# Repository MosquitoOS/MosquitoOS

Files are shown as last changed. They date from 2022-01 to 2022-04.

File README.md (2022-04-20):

# MosquitoOS

Ceci est le répertoire du projet Mosquito Opensource.

A l'exeption des composants vélos (roues, pédalier, moyeux, freins, etc.) tous les composants du Mosquito sont sous licence libre `CERN Open Hardware Licence Version 2 - Weakly Reciprocal`.

Consommables		                    Observations	                                                    fournisseur			
epoxy		                            Epoxy Resin L + Hardener CL (60 min) kit/ 930 g non cytotoxique	    https://shop1.r-g.de/en/art/109285-AP		
charges fibres cellulose pour collages	                        		                                    sicomin			
colle SADER vinylique a bois rapide exterieur	9.1	collage cp sur styrodur	magasin bricolage			
tresse verre diametre 20mm x5m			                                                                    https://shop1.r-g.de/en/art/201100			
tresse fibre de verre diametre 45mm x5m			                                                            https://shop1.r-g.de/en/art/201105
ruban carbone UD 250g/sqm 25mm 10m			                                                                https://shop1.r-g.de/en/art/200159-25			
DPP™ Carbon rectangular rod (10.0 x 1.0) 1000 mm x4	                                                        https://shop1.r-g.de/en/art/750302					
demoulant PVA 250ml 						
ruban peel ply 20mm 100m						
tissus fin verre 55g/sqm 10m		    pour marouflage sur carenage carton	                                https://shop1.r-g.de/en/art/G-0055097-LW
pinceau agent demoulage						
spatules			                                                                                        https://shop1.r-g.de/en/art/325100
rouleau essuis tout (industriel)						
gants 					
tissus d'arachage et scotch et film retractable						
mousse styrodur		                    plaque magasin bricolage ep 20mm env 10 euros				
contre plaque marine ou aviation	    95.12euros	cp aviation 1500x500mm ep1.5 prix=45euros+port, 1.5m2 devrait suffire	https://jr-contreplaque.fr			
plaque carton ep 2 ou 3mm		        env 7m2 pour le carenage				
scotch papier pour carton						
plaque carton epaisse (nidabeille)pour les couples		ep15mm plaque 800x600 env4 plaques 5euros/plaque	
Colle loctite 648 pour ficher les roulements								https://www.scootfast.net/loctite-bearing-sealant-5-ml.html

plaques aluminium 1 et 1.5mm			https://www.blockenstock.fr/epaisseur-5-8mm-c102x3032238			
tube alu diam25 lg 1m		            pour direction et divers				
tube diam22.2	                        recup velo				

boulons, divers quincaillerie						
6 rotules M8 LH et 6 rotules M8 RH	25.4 Euros sur ebay.co.uk provenance chine 3euros piece	remarque bis : prendre du M6 moins cher moins lourd			
tige filetee M8 LH	5	                5euros/250mm chine				
tige filetee M8 RH	5					
6 ecrous a gauche M8	                6.78 Euros Metric RH / LH Threaded Half Nuts Ideal for Rod End Rose Joint - Packs x5 or x10			
roulements a billes 37x25x7 6805-2rs	8 Euros	ebay ou 123roulements.fr			
charnieres a billes x4	                23 Euros	2pcs Door Hinge Durable Ball Bearing Thickened Stainless Steel Replacement Parts	ebay			
impression plans A0	                    netprinter.co.uk			
						
matos velo						
1 cadre vtt 26" bases et haubans cintres	40	leboncoin				
1 jeu de pedalier square taper	0	recup sur vtt mbk le boncoin				
1 pedalier (manivelles courtes) 	30					
plateau 130bcd env 42 dents	0					
2 pedales						
1 chaine						
1 pignon pour nexus	15	a confirmer				
1 moyeu nexus rollerbrake	30	remarque 150euros si neuf port compris inclus pignon poignee tournante et ecrous				
switching unit for nexus 8 	15	besoin reference exacte				
rondelles de sécurité pour des pattes de cadre verticales (bleue 8R / verte 8L)						
1 jeu de direction		provenant du cadre vtt 				
1 potence reglable longue (type tandem passager)		ou bien stratification sur tube alu				
1 guidon hamster		idem, bricolage de tubes				
ou 1 guidon carbone a recouper modifier						
2 poignees de frein 						
1 repartiteur de freinage		a fabriquer				
1 changement de vitesse pour nexus						
2 poignees mousse ou guidoline de guidon						
3 gaines de freins + 3 cables de freins 						
1 gaine de derailleur et cable de derailleur		sur le cadre de vtt				
4 tendeurs ajustage tension de cable frein et derailleurs						
2 jantes 20" 28H pour roue arriere	40	jante exal tx19				
1 jante 20" 32ou36H? pour nexus						
56rayons roue arriere et 56 tetes de rayon laiton	23	0.45euro/piece				
32 ou 36 rayons roue avant						
2 moyeux freins a tambour sturmey archer	140	70euros piece				
2 axes inox pour roue arriere 						
3 chambres a air						
3 pneus						
						
total appros	927.6 Euros					

Information issue de https://ethercalc.net/budget-workshop-mosquito

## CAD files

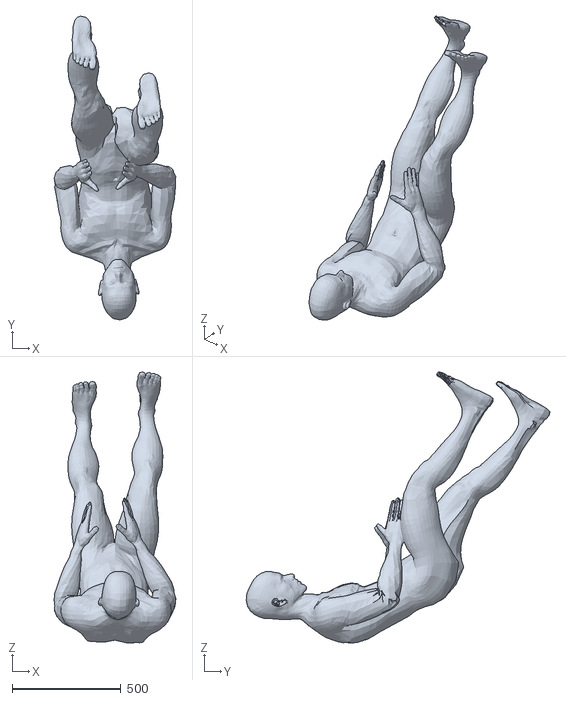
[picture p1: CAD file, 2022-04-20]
dorian3d_recumbent_position.stl
559.3 x 1394.2 x 1244.1

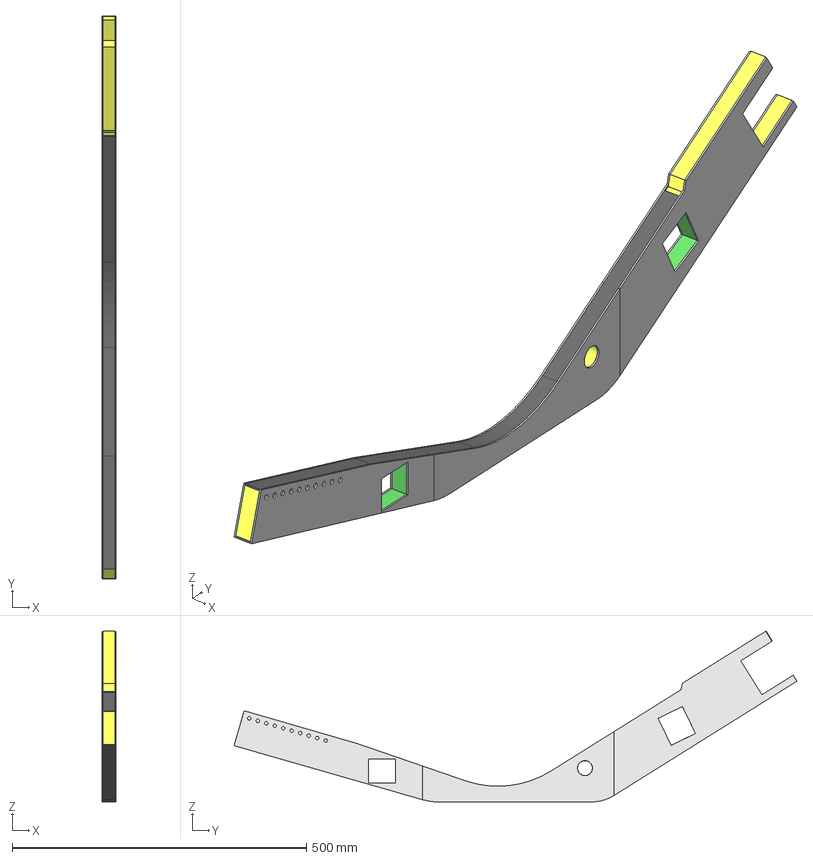
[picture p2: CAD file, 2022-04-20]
longerontempWIP.FCStd
24.0 x 956.3 x 290.5 mm
mousse
Tasseau06
Support_axe_biellettes
Tasseau04
Tasseau03
Tasseau05
Tasseau02
Tasseau01
Carbone_bas
Carbone_Haut
Cp_avant
Cp_milieu
Cp_arriere

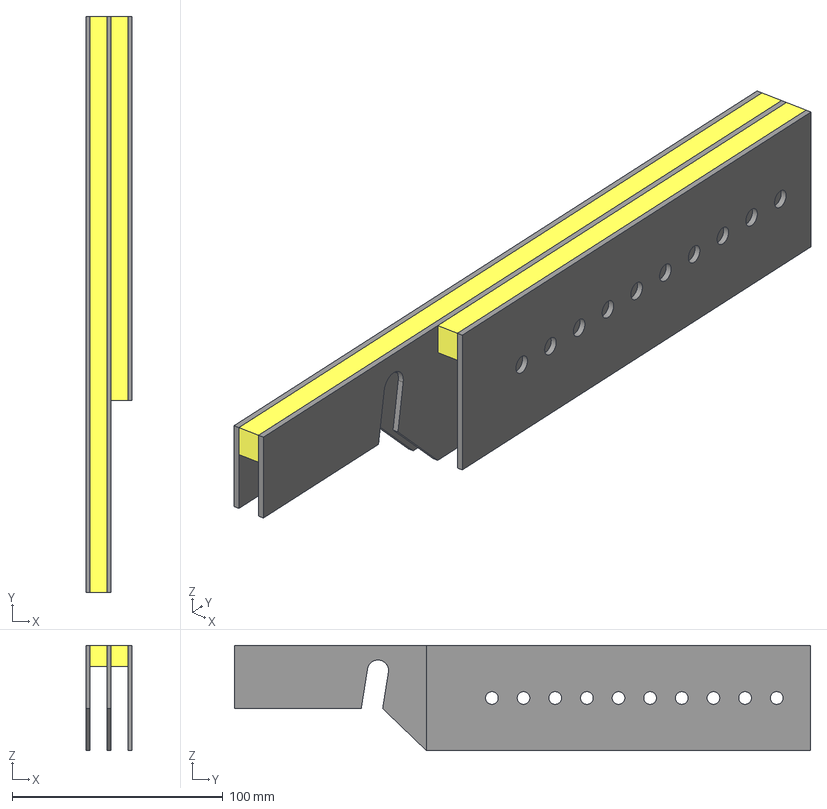
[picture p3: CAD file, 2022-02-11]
patte_avant_gauche_support_roue_avant.FCStd
22.0 x 273.0 x 50.0 mm
Tasseau01
Long_alu_peau_01_02
Tasseau_06
Court_Alupeau_03

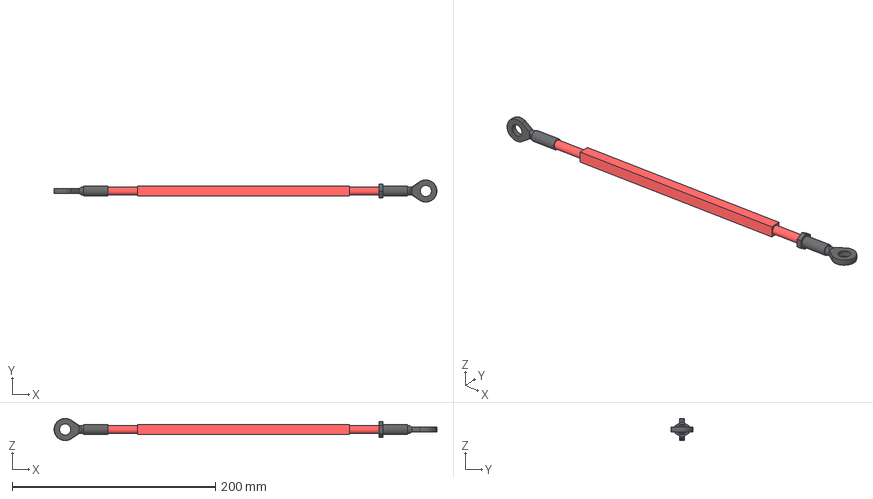
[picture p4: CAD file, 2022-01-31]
bielle_grande_(355_mm_entre_axe).FCStd
377.0 x 21.9 x 21.9 mm
Bout de bielle
Partie centrale de la bielle
Bout de bielle 2

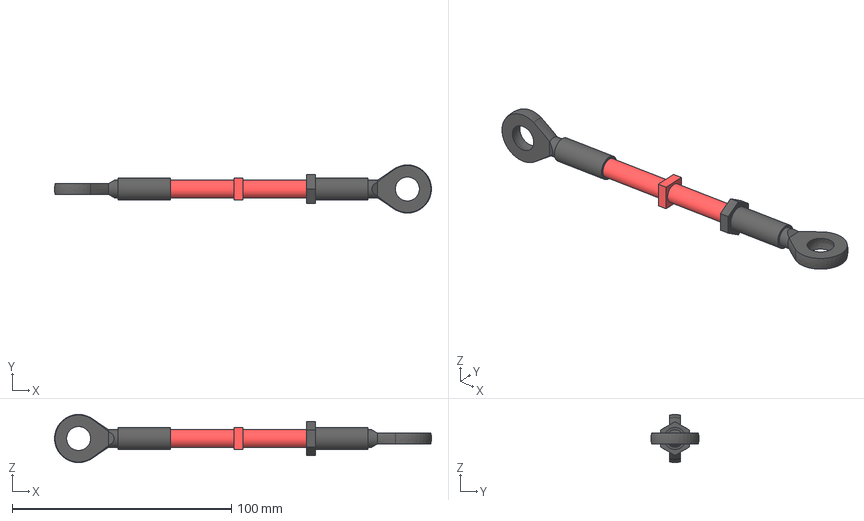
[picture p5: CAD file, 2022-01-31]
bielle_(150_mm_entre_axe).FCStd
172.0 x 21.9 x 21.9 mm
Bout de bielle
Partie centrale de la bielle
Bout de bielle 2

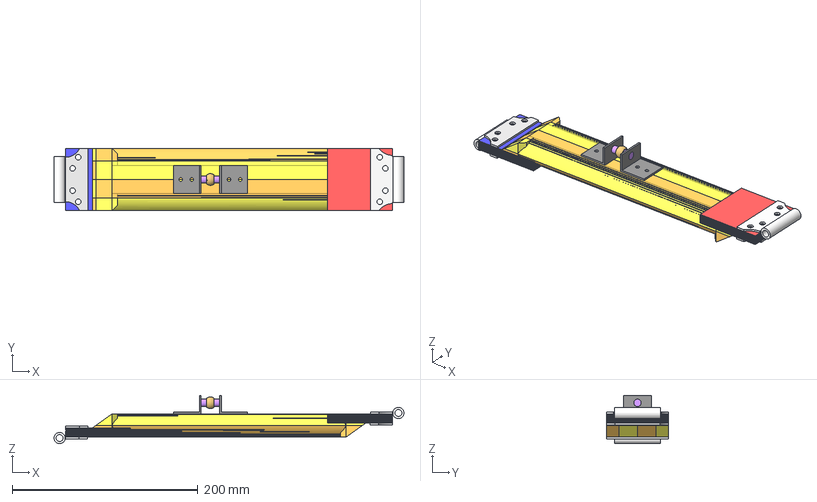
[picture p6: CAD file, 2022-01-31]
barre_de_direction.FCStd
377.0 x 67.0 x 52.0 mm
Barre de direction (corps)001
Pièce d'extrémité 2 N°3/010
Pièce d'extrémité 1 N°7/010
Pièce d'extrémité 1 N°6/010
Pièce d'extrémité 1 N°1/010
Pièce d'extrémité 2 N°8/010
Pièce d'extrémité 2 N°5/010
Pièce d'extrémité 1 N°4/010
Ogive de bielle002
Charnière 003
Piece contrefort de la charnière 003
Pièce d'extrémité 1 N°8/010
Pièce d'extrémité 1 N°9/010
Piece contrefort de la charnière 004
Ogive de bielle003
Cornière 004
Cornière 003
Charnière 004
Pièce d'extrémité 2 N°4/010
Pièce d'extrémité 2 N°6/010
Pièce d'extrémité 1 N°2/010
Pièce d'extrémité 2 N°2/010
Pièce d'extrémité 2 N°9/010
Pièce d'extrémité 2 N°1/010
Pièce d'extrémité 2 N°7/010
Axe de l'ogive001
Pièce d'extrémité 1 N°5/010
Tasseau 1
Tasseau 2
Tasseau 3
Tasseau 4
Tasseau 5
Tasseau 6
Tasseau 7
Tasseau 8

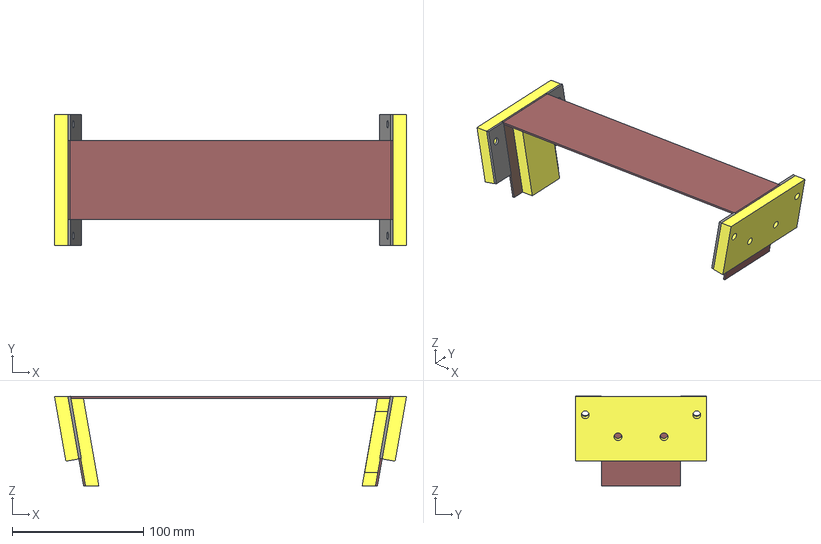
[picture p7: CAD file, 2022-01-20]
attache_bielle_alternative.FCStd
268.3 x 100.0 x 68.4 mm
Tasseau_bois
Cp_exterieur001
Cp_exterieur002
Cp_bois_10mm_ep
Tasseau_bois003
Body009 (mirrored)
Alu_2mm
Alu_2mm001

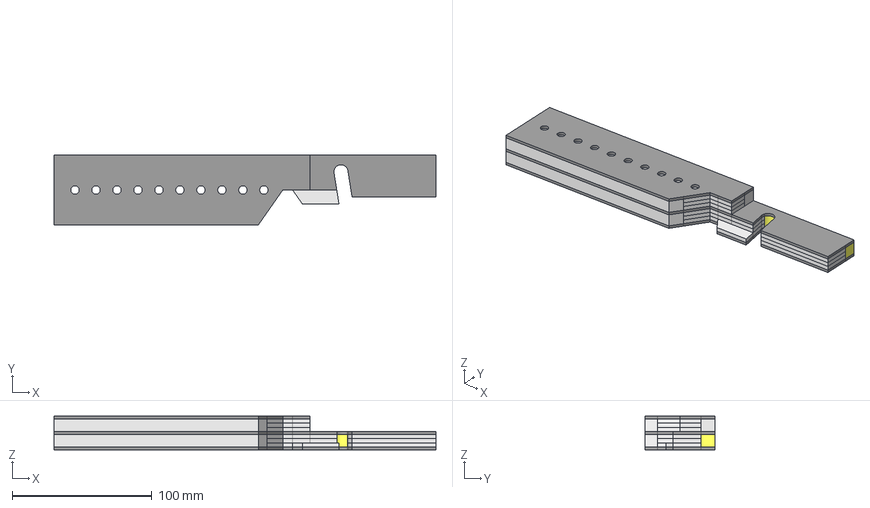
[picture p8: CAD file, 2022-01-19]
patte_avant_droite.FCStd
273.0 x 50.0 x 24.0 mm
cp_45_deg_1.1
aluminium_ext
aluminium_inter
semelle_supp_1
cp_0_deg_1.1
cp_45_deg_2
semelle_inf_1
cp_90_deg_2
aluminium_milieu
cp_90_deg_1.1
cp_90_deg_1.002
cp_45_deg_1.002
cp_0_deg_1.002
semelle_inf_002
semelle_supp_002
cp_0_deg_2

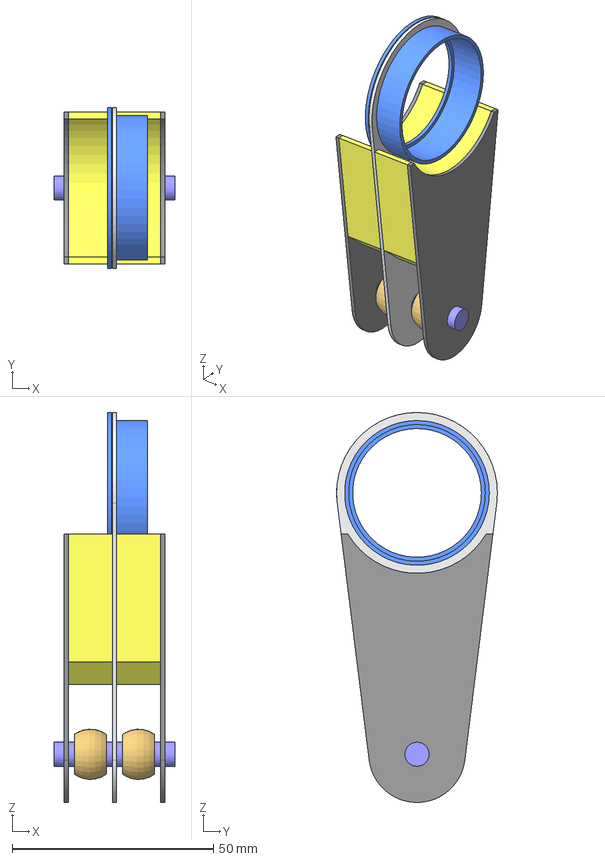
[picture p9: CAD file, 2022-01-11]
guignol_intermediaire.FCStd
30.0 x 40.0 x 97.0 mm
Pièce centrale
Pièce annexe 1
Pièce d'extrémité 1
Pièce annexe 2
Pièce d'extrémité 2
Ogive de bielle
Ogive de bielle (clone)
Goupille
Piece de maintien sur le roulement

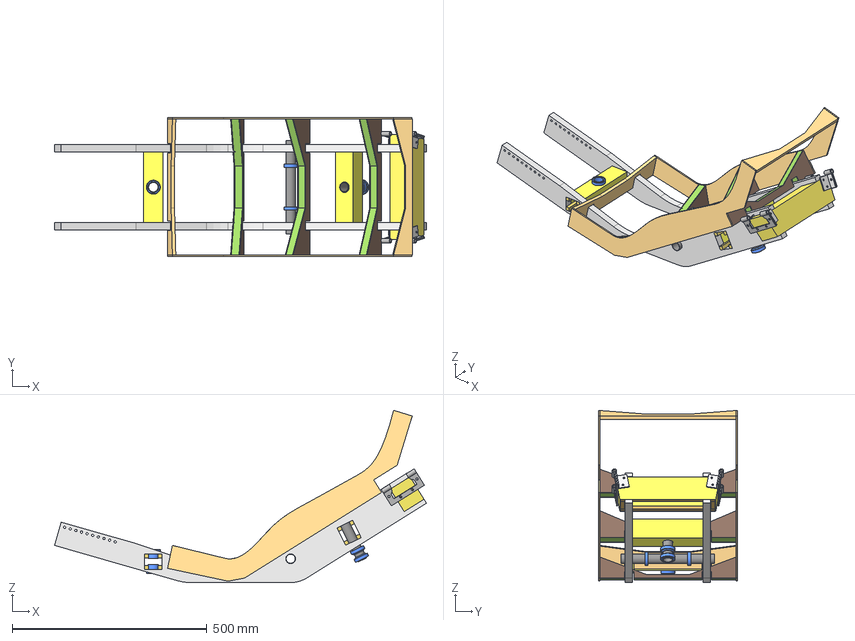
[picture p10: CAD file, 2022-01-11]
chassis_du_trike.FCStd
954.0 x 356.0 x 442.1 mm
traverse
Roulement 003
Roulement 004
traverse haut
Tasseaux intérieurs 1
Tasseaux intérieurs 2
Cornière 1
copie de cornière1
Cornière 2
Copie de cornière 2
Charnière
Charnière clone
Tasseau intèrieur 3
Tasseau intèrieur 4
Tasseau005
Enveloppe001
Tasseau006
Tasseau007
Tasseau008
Roulement
Roulement clone
Tasseau
Enveloppe
Tasseau2
Tasseau3
Tasseau4
Axe central
Roulement 1
Roulement 2
corps du longeron
longeron 2 clone0
Couple01
Longerons_siege
Longeron02_CP_01
Longeron02_mousse
Longeron02_CP_02
Longeron03_CP_01
Longeron03_mousse
Longeron03_CP_02
Longeron04_CP_01
Longeron04_mousse
Longeron04_CP_02
Longeron05

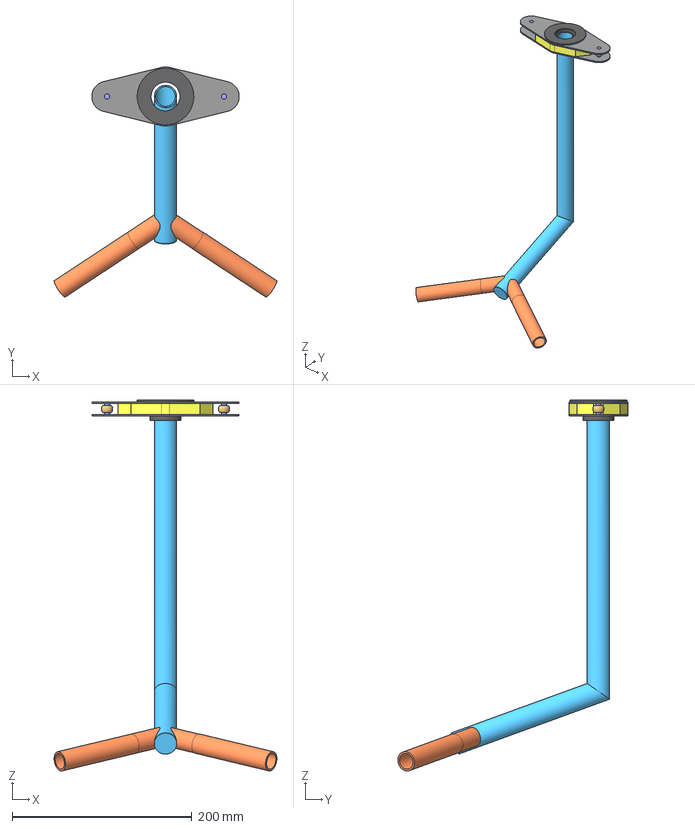
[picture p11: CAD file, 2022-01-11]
guignol_avant_et_guidon.FCStd
247.7 x 256.1 x 412.6 mm
Plaque métallique
Plaque intercalaire
Plaque métaliique (clone)
Ogive de bielle
Ogive de bielle (clone)
Goupille
Goupille (clone)
Plaque de maintient
Guidon 1
Guidon 2
Guidon 3

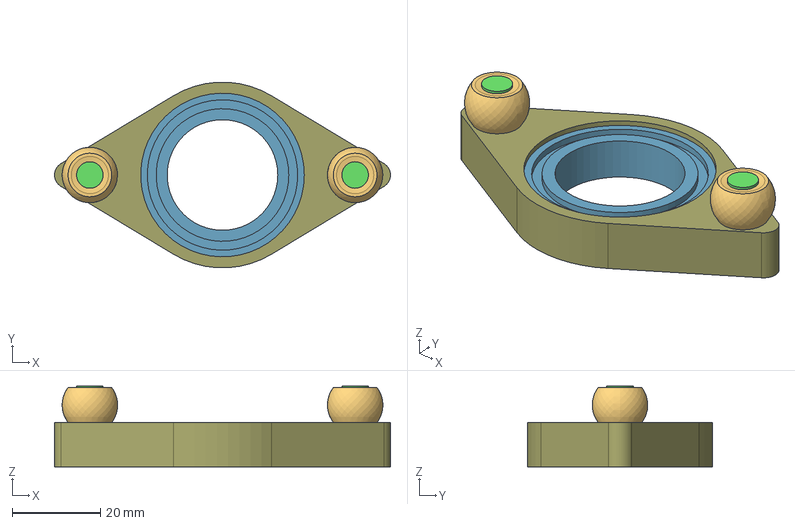
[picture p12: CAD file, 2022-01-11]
guignol_a_l_arriere.FCStd
76.0 x 41.9 x 18.3 mm
Guignol
Picot extrémité du guignol
Picot extrémité du guignol 2 (clone)
Roulement
Ogive de bielle
Ogive de bielle clone

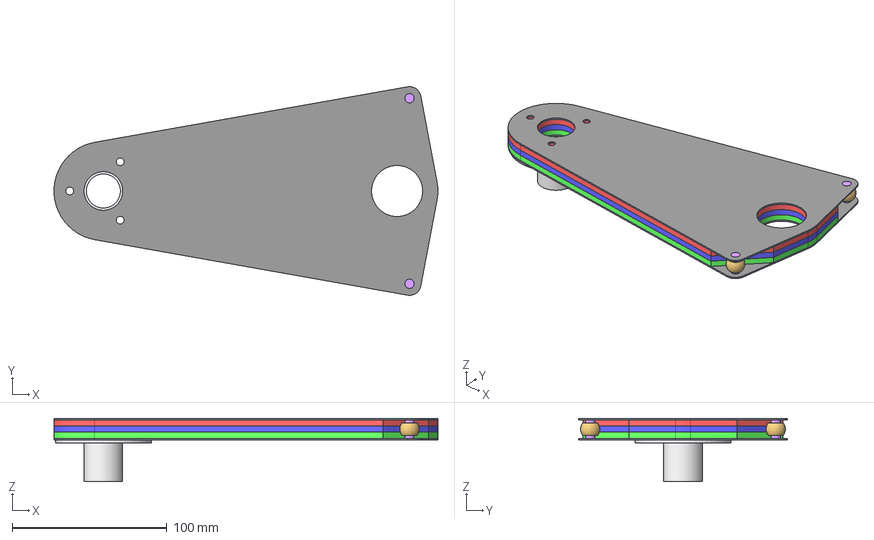
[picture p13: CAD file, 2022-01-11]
secteur_de_bielles.FCStd
248.4 x 135.0 x 41.0 mm
Plaque d'aluminium
Plaque contreplaqué intercalaire fibre de surface à 0° d'angle (axe x)
Plaque contreplaqué intercalaire fibre de surface à 90° d'angle (axe x)
Plaque contreplaqué intercalaire fibre de surface à 45° d'angle (axe x)
Plaque d'aluminium (clone)
Ogive de bielle
Ogive de bielle clone
Axe de l'ogive
Axe de l'ogive clone
Pièce support du guignol

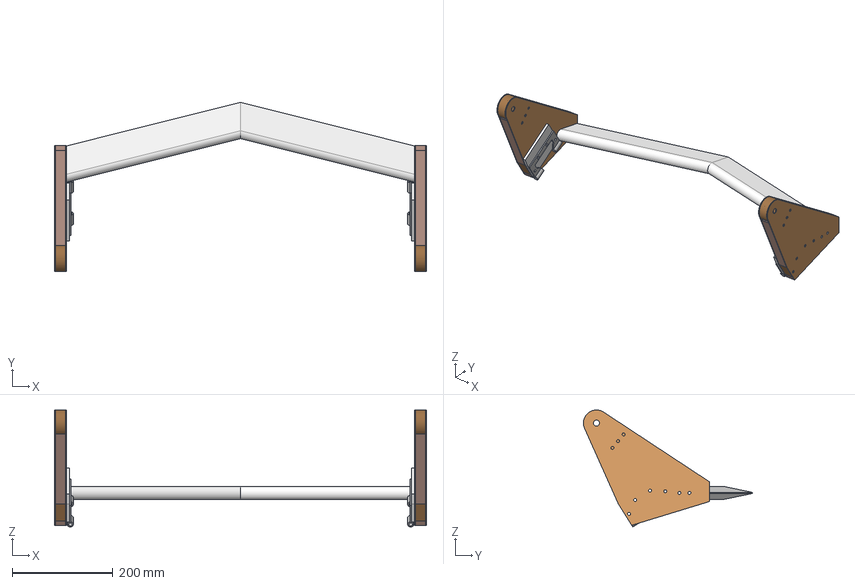
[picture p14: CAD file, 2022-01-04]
essieu.FCStd
740.0 x 336.6 x 232.7 mm
Boomerang
CP_peau_int001
ergot004
ergot003
Tasseau_004
Tasseau_003
Tasseau005
Tasseau006
Mousse001
CP_peau_ext001
CP_support_axe001
CP_support_bielle001
Calle_bielle001
Gond001
CP_peau_int
ergot01
ergot02
Tasseau_01
Tasseau_02
Tasseau03
Tasseau04
Mousse
CP_peau_ext
CP_support_axe_01_00
CP_support_axe
CP_support_bielle
Calle_bielle
Gond

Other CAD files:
roue_arriere.FCStd
bielle_intermediaire_(220mm_entre_axe).FCStd

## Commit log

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2021-12-28 Delete Assemblage barre de direction et cornière.FCStd
    Pas besoin de cet assemblage on ajoute directement les cornière et autres charnières dans les fichiers pour limiter l'assemblage
    [Assemblage barre de direction et cornière.FCStd]
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2021-12-28 Add files via upload
    Version 2 les charnières, cornières, ogives de bielles sont intégrées. Les plaques de contre plaqué sont apparentes et idem pour les tasseau de construction.
    [Barre de direction.FCStd]
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2021-12-28 Add files via upload
    Ajout des charnières et des renforts sur les cotés (tasseaux), réajustement des trous, perçages des trous sur le longeron
    [longeron infèrieur.FCStd]
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2021-12-28 Add files via upload
    Ajout du guignol arrière avec les ogives de bielle et le roulement
    [Guignol à l'arrière.FCStd]
2021-12-28 Add files via upload
    Le fichier était vide, j'ai modifié cette version. Elle doit être intégrées dans les fichiers.
    [Bielle_ogive.FCStd]
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2021-12-30 Assemblage_essieux
    Import de la calle et d'une partie du gond dans le fichier
    [essieuD.FCStd, essieuG.FCStd]
2021-12-31 Add files via upload
    Ajout du Guignol intermediaire
    [Guignol intermediaire.FCStd]
2021-12-31 Add files via upload
    Longeron qui vient supporter le guignol intermediaire
    [Longeron de transmission de bielles.FCStd]
2021-12-31 Add files via upload
    Ajout du longeron intermédiaire avec son axe central
    [longeron intermédiaire.FCStd]
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2022-01-01 Add files via upload
    Ajout système guignol guidon
    [Guignol à l'avant (guidon).FCStd]
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2022-01-03 Add files via upload
    Ajout fichier essieu qui inclut essieud, essieug et boomerang
    [essieu.FCStd]
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2022-01-03 Add files via upload
    Barre de direction V3
    [barre_de_direction.FCStd]
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2022-01-03 Add files via upload
    changement de nom b minuscule et trait bas à la place des espaces
    [Bielle_intermediaire_(220mm_entre_axe).FCStd, bielle_(150_mm_entre_axe).FCStd, bielle_grande_(355_mm_entre_axe).FCStd]
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2022-01-04 Add files via upload
    Ajour secteur de bielles, tout nickel avec part included
    [secteur_de_bielles.FCStd]
2022-01-04 Delete Bielle_ogive.FCStd
    Cette piece n'est plus nécessaire, elle est inclue dans tous les fichiers nécessitants !
    [Bielle_ogive.FCStd]
2022-01-04 Add files via upload
    Modification de nom à l'interieur du fichier traverse au lieu de longeron dans le corps
    [traverse_de_transmission_de_bielles.FCStd]
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2022-01-04 Add files via upload
    Les fichiers spreadsheets n'était pas intégrés dans les parts... c'est fait maintenant !
    [essieu.FCStd]
2022-01-04 Add files via upload
    Ajout de part dans le part pour effectivement tout avoir statique à l'assemblage (j'espère)
    [essieu.FCStd]
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2022-01-04 Add files via upload
    rectification angle de 15 à 16° et changement des cotes pour les traverses
    [longeron_provisoir_pour_test_assemblage.FCStd]
2022-01-04 Add files via upload
    changement sur le longeron donc changement du fichier
    [chassis_du_trike.FCStd]
2022-01-04 Add files via upload
    Modification V2 par Forthman. Je comprends pas ce qu'il a fait de plus... on verra cela avec lui ce week end...
    [secteur_de_bielles .FCStd]
2022-01-04 Add files via upload
    Version avec le nom d'origine. Donc je disais c'est une version modifiée par forthman. on le vois ce week-end normalement
    [secteur_de_bielles.FCStd]
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2022-01-05 Add files via upload
    inclusion du siege (il ne se place pas correctement, il y a un soucis quelque part...)
    [chassis_du_trike.FCStd]
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2022-01-11 Add files via upload
    Modification du trou de bielle de 8 mm de diamètre à 6 mm (les vis que l'on a utilisé pour le montage)
    [secteur_de_bielles.FCStd]
2022-01-11 Add files via upload
    Modification du diamètre des trous d'ogive de bielle de 8mm de diamètre à 6 mm
    [guignol_a_l_arriere.FCStd]
2022-01-11 Add files via upload
    Modification du diamètre des trous d'ogive de 8mm à 6mm
    [guignol_avant_et_guidon.FCStd]
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2022-01-11 Add files via upload
    Modification du diamètre des ogives de 8 à 6 mm et de la pièce de maintien du roulement pour s'adapter à l'existent (sans prise de mesure réelle)
    [guignol_intermediaire.FCStd]
2022-01-11 Add files via upload
    Modification du diamètre des roulements sur la traverse de transmission de bielle
    [chassis_du_trike.FCStd]
2022-01-11 Add files via upload
    Re modification du diamètre du roulement plus réaliste
    [guignol_intermediaire.FCStd]
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2022-01-31 Add files via upload
    Espacement entre le bord de piece de 15 mm au lieu de 16 et correction des espacements qui était de 17mm au lieu de 15mm
    [patte_avant_gauche_support_roue_avant.FCStd]
2022-01-31 Add files via upload
    modification de l'ogive de bielle maintenant la sphere est sur l'axe au lieu d'être décalée (précédemment freecad ne pouvait pas le mettre sur l'axe, trop de contraintes !?)
    [barre_de_direction.FCStd]
2022-01-31 Add files via upload
    Décalage de la tête de 90° par rapport à l'autre, à cause de l'assemblage au trike
    [bielle_(150_mm_entre_axe).FCStd]
2022-01-31 Add files via upload
    Décalage de la tête de 90° pour assemblage correcte.
    [bielle_grande_(355_mm_entre_axe).FCStd]
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2022-02-13 Add files via upload
    Nomenclature et traduction en anglais de la nomenclature
    [nomenclature et traduction.ods]
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2022-02-13 Add files via upload
    Ajout de dorian 3d format stl beaucoup plus leger au moins 60 fois moins qu'un step.
    [dorian3d_recumbent_position.stl]
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
